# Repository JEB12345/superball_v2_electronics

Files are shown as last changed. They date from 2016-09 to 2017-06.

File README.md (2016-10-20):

# superball_v2_electronics

This repo houses all the electronic boards used in the SUPERball V2 tensegrity robot prototype.

List of PCB boards:
 - Main control board (ToDo)
 - Power control board (ToDo)
 - 10 pin Molex extension board
 - Battery connector conversion board (ToDo)

Main control board features:
 - Intel Edison Interface
 - DWM 1000 Module
 - Status LEDs (RGB and single color)
 - dsPIC33E (or lower uC?)

Power control board features:
 - Main power input of 25.2V - 22.1V
 - Regulate main power down to either 5.5 or 3.3V (do we need 5.5 regulation anymore?)
 - Backup batter support (either coincell or lipo?)
 - Power safety features all ANDed together:
   + Wireless killswitch - NRF24L01
   + manual switch
   + uC/Edison up signal
   + 24V present
 - Voltage and Current monitoring (do we need with with the Hebi motors?)
 - ??? Battery Management system per NASA requirements?

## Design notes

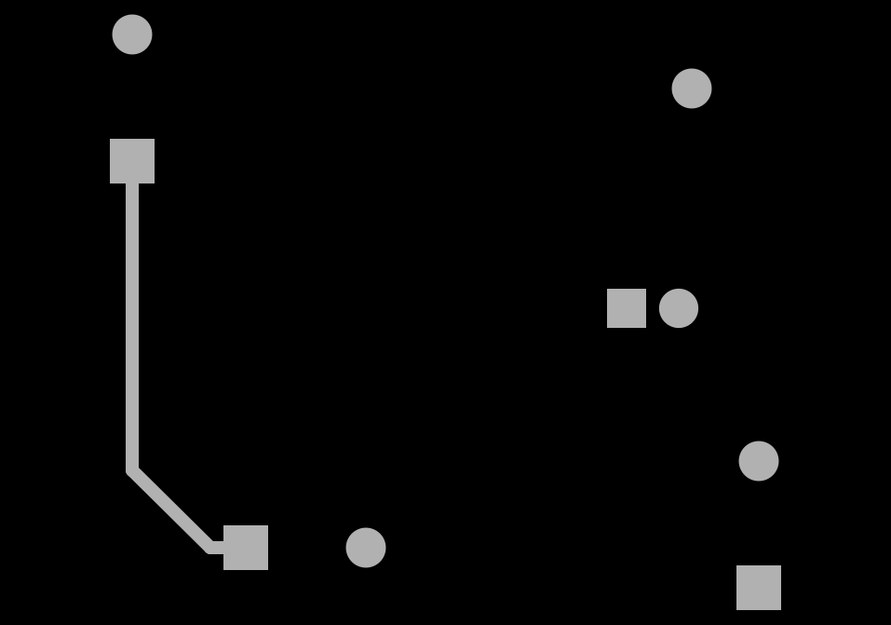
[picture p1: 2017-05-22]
main_master_dev_boards/power_systems/power_on_switch/Gerber/power_on_switch-BCu.png

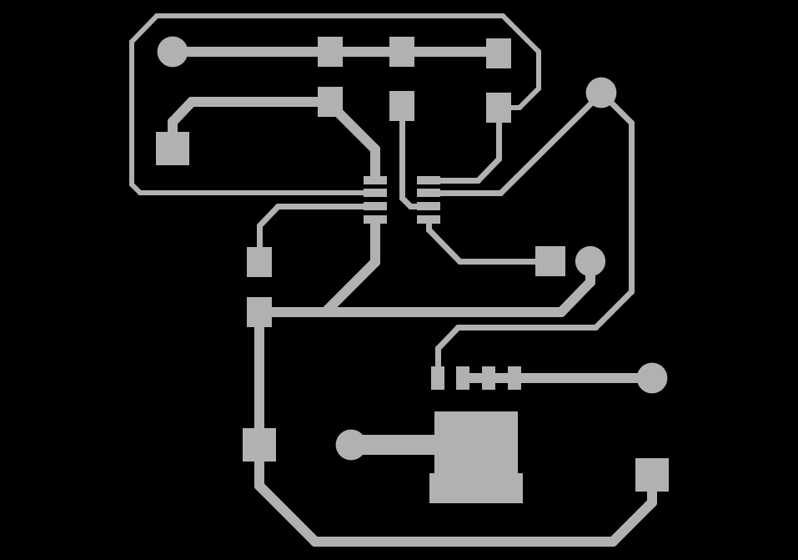
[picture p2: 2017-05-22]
main_master_dev_boards/power_systems/power_on_switch/Gerber/power_on_switch-FCu.png

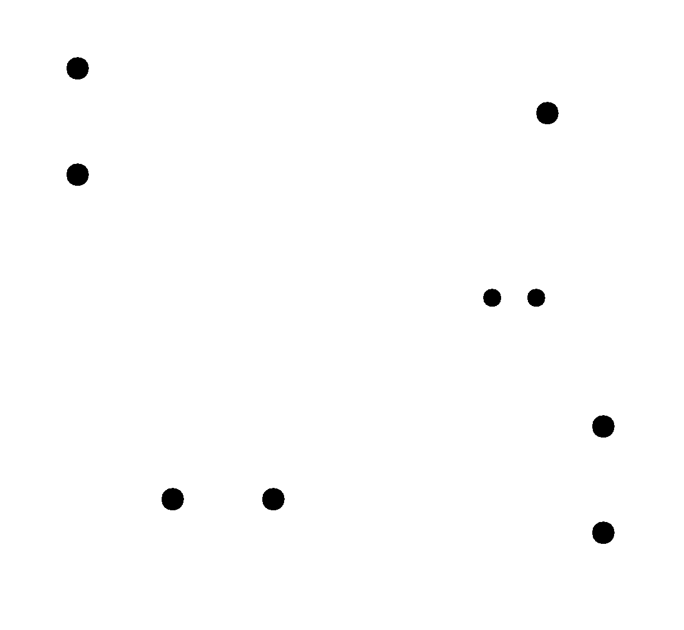
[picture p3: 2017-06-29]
main_master_dev_boards/power_systems/power_on_switch/Gerber/power_on_switch_drl_BW_edge.png

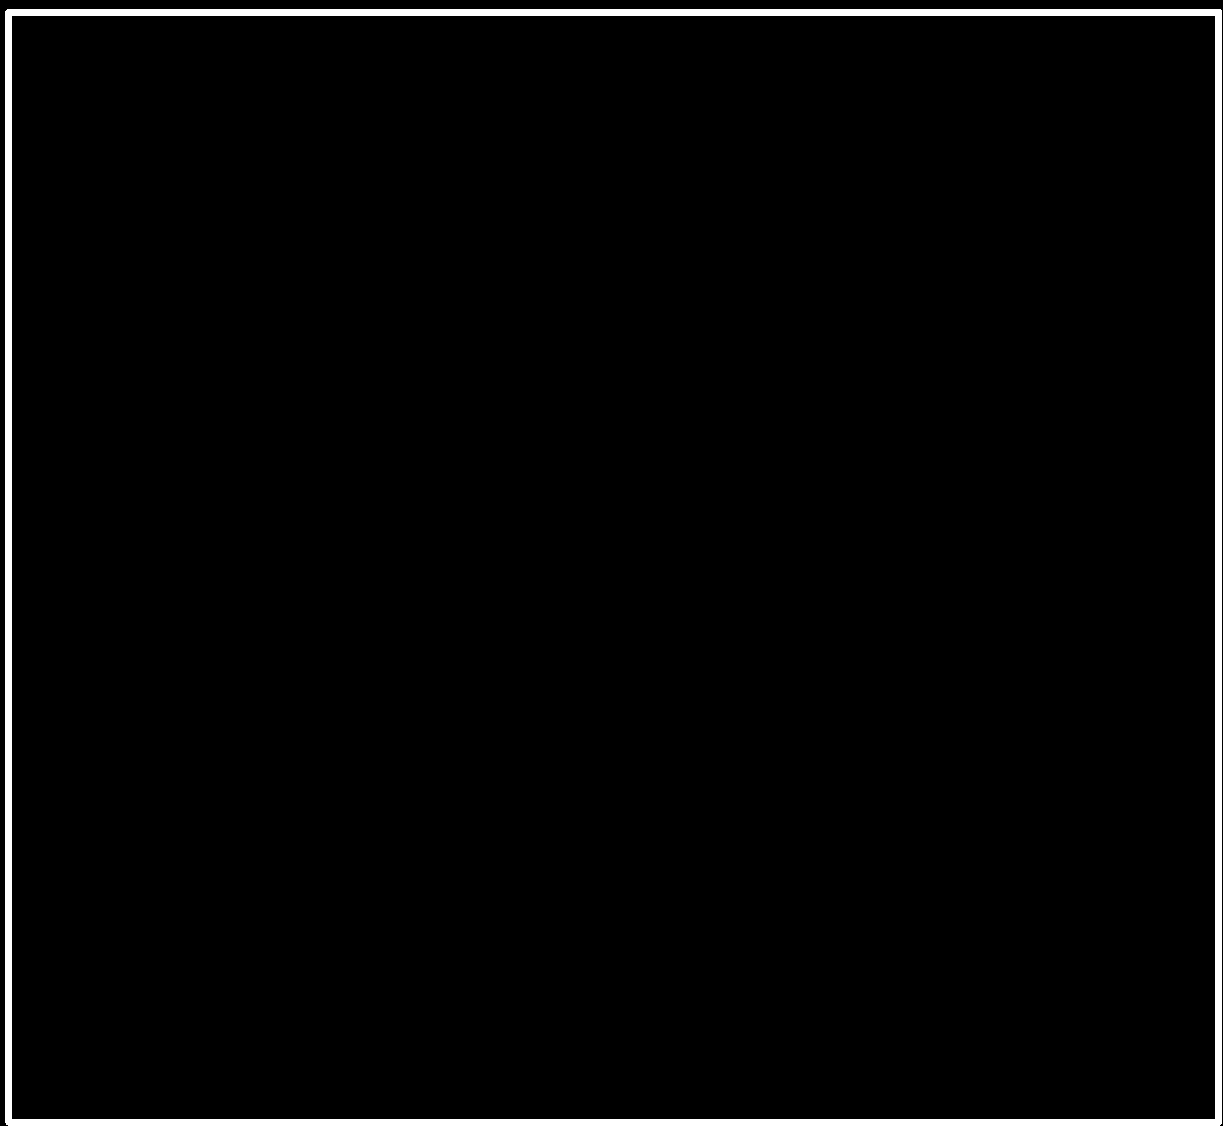
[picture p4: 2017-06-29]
main_master_dev_boards/power_systems/power_on_switch/Gerber/power_on_switch-EdgeCuts_BW.png

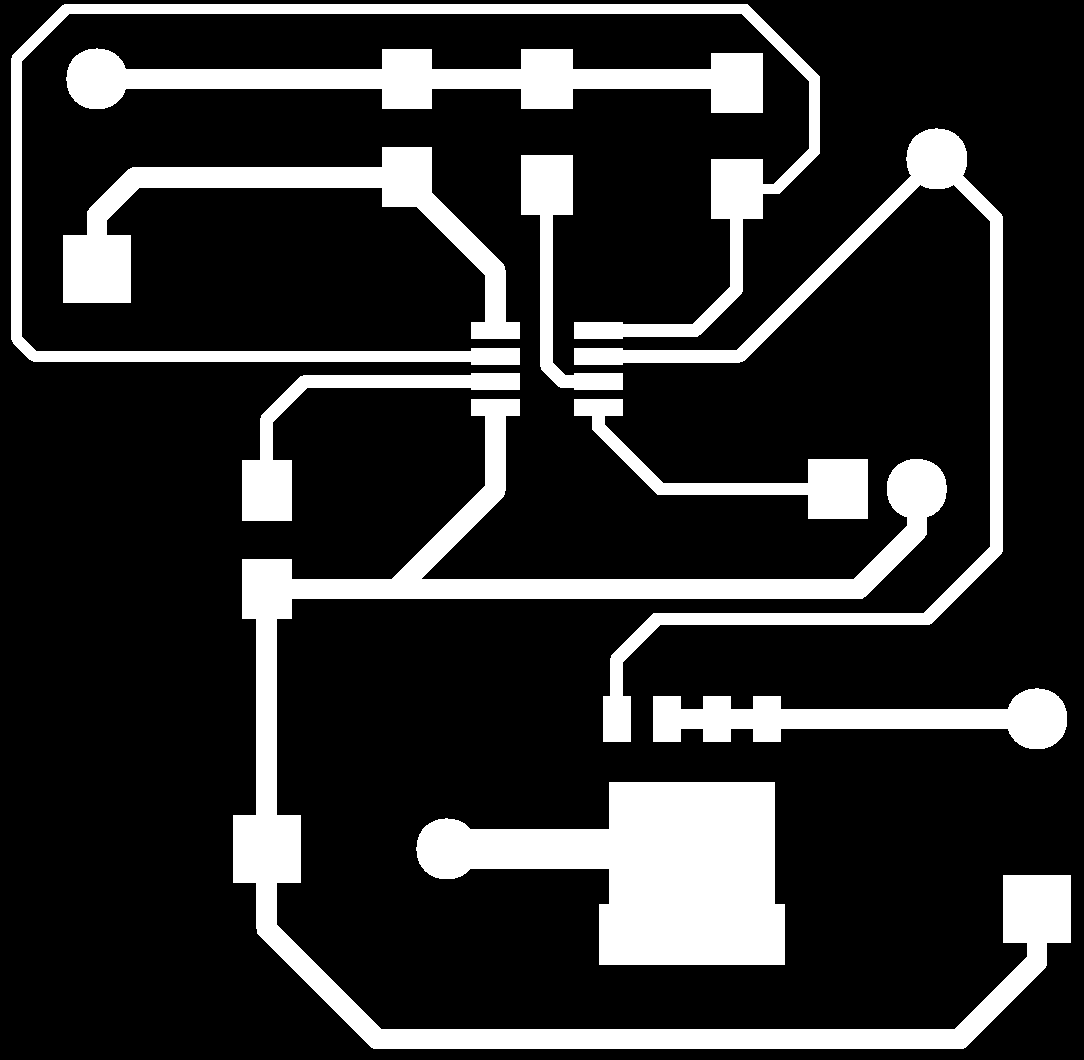
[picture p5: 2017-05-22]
main_master_dev_boards/power_systems/power_on_switch/Gerber/power_on_switch-FCu_BW.png

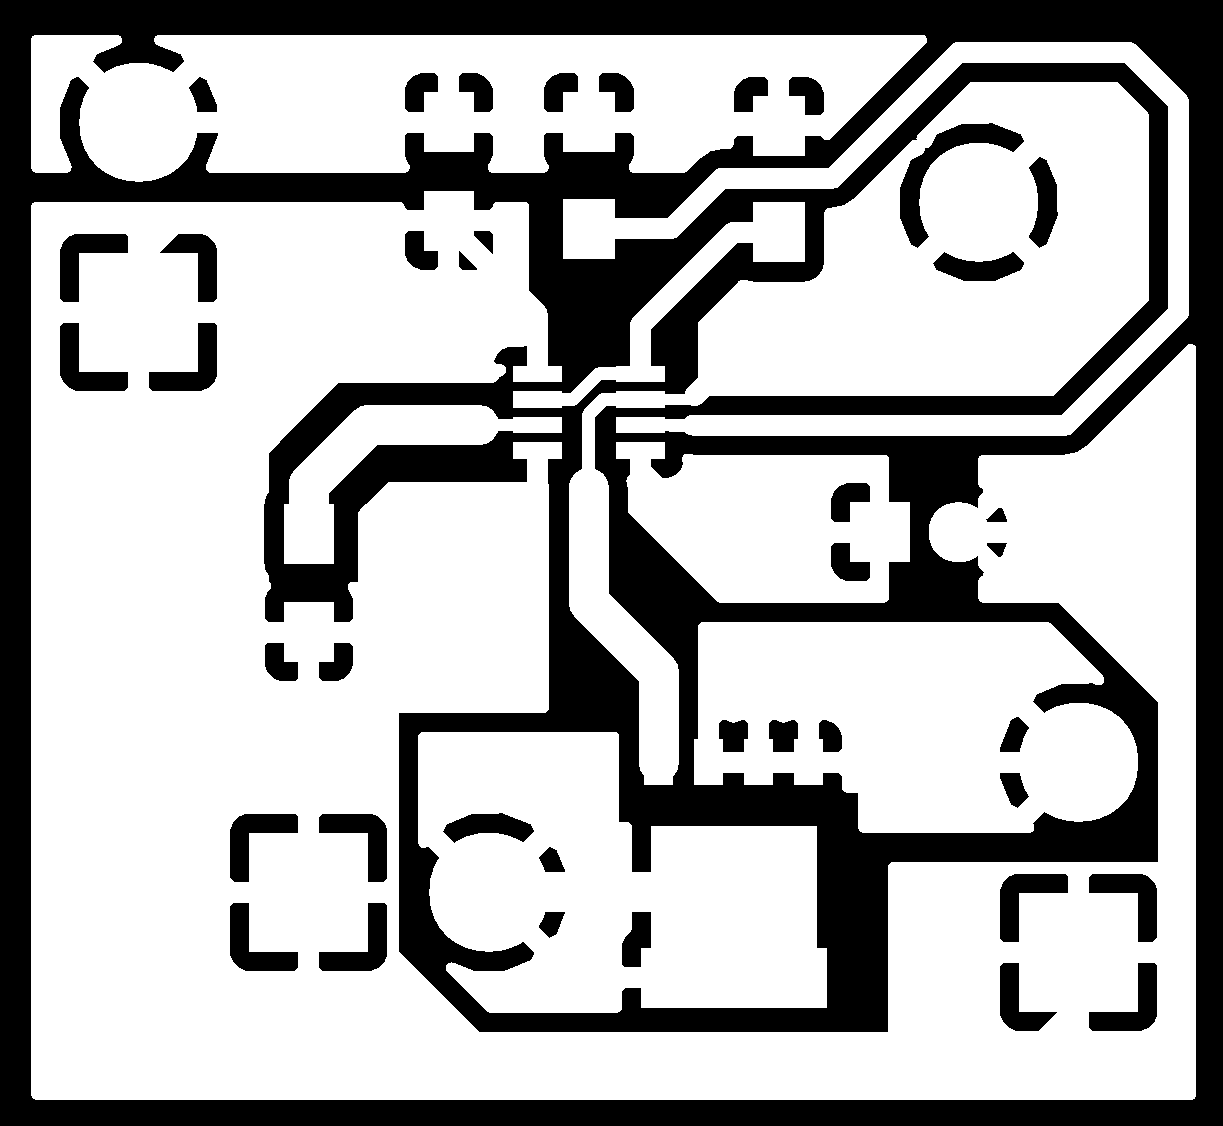
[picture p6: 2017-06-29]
main_master_dev_boards/power_systems/power_on_switch/Gerber/power_on_switch-FCu_BW_edge.png

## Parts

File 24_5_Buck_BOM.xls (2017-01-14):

Part | Manufacturer | Part Number | Quantity | Price | Attribute 1 Name | Attribute 1 Value | Attribute 2 Name | Attribute 2 Value | Attribute 3 Name | Attribute 3 Value | Footprint
Cboot | Kemet | C0805C104K5RACTU | 1 | 0.01 |  |  |  |  |  |  | 0805
Cin | TDK | C1005X5R1V225K050BC | 1 | 0.06 |  |  |  |  |  |  | 0402_065
Cout | TDK | C2012X5R1A336M125AC | 1 | 0.29 |  |  |  |  |  |  | 0805
D1 | Fairchild Semiconductor | SS24FL | 1 | 0.07 | VFatIo | 0.55V | Io | 2A | VRRM | 40V | SOD-123F
L1 | Bourns | SRN8040-150M | 1 | 0.22 | L | 15uH | DCR | 0.07Ohm | IDC | 2.4A | SRN8040
Rfbb | Yageo America | RC0603FR-0712KL | 1 | 0.01 | Resistance | 12kOhm | Tolerance | 1% | Power | 0.1W | 0603
Rfbt | Yageo America | RC0603FR-0768KL | 1 | 0.01 | Resistance | 68kOhm | Tolerance | 1% | Power | 0.1W | 0603
Rt | Vishay-Dale | CRCW040245K3FKED | 1 | 0.01 | Resistance | 45.3kOhm | Tolerance | 1% | Power | 0.063W | 0402
U1 | Texas Instruments | LMR16030PDDAR | 1 | 1.95 |  |  |  |  |  |  | DDA0008E_N
Cff | Kemet | C0805C270J5GACTU | 1 | 0.01 |  |  |  |  |  |  | 0805

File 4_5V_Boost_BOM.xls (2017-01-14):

Part | Manufacturer | Part Number | Quantity | Price | Attribute 1 Name | Attribute 1 Value | Attribute 2 Name | Attribute 2 Value | Attribute 3 Name | Attribute 3 Value | Footprint
Cin | Taiyo Yuden | JMK212BJ226MG-T | 1 | 0.05 |  |  |  |  |  |  | 0805
Cout | TDK | C3216JB1A476M | 1 | 0.3412 |  |  |  |  |  |  | 1206
Css | MuRata | GRM155R71C153KA01D | 1 | 0.01 |  |  |  |  |  |  | 0402
L1 | Vishay-Dale | IHLP2020BZER1R0M11 | 1 | 0.99 | L | 1uH | DCR | 0.018Ohm | IDC | 7A | IHLP-2020BZ
U1 | Texas Instruments | TPS61232DRCR | 1 | 0.95 |  |  |  |  |  |  | DRC0010G

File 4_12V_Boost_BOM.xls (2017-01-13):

Part | Manufacturer | Part Number | Quantity | Price | Attribute 1 Name | Attribute 1 Value | Attribute 2 Name | Attribute 2 Value | Attribute 3 Name | Attribute 3 Value | Footprint
Cbst | MuRata | GRM155R61A104KA01D | 1 | 0.01 |  |  |  |  |  |  | 402
Ccomp | MuRata | GRM033R71C181KA01D | 1 | 0.01 |  |  |  |  |  |  | 201
Ccomp2 | MuRata | GRM1555C1H9R1CA01D | 1 | 0.01 |  |  |  |  |  |  | 402
Cin | Taiyo Yuden | LMK212BJ106KG-T | 3 | 0.02 |  |  |  |  |  |  | 805
Cin2 | MuRata | GRM155R60J104KA01D | 1 | 0.01 |  |  |  |  |  |  | 402
Cout | MuRata | GRM31CR71E106KA12L | 2 | 0.05 |  |  |  |  |  |  | 1206_190
Cvcc | MuRata | GRM188R61A225KE34D | 1 | 0.02 |  |  |  |  |  |  | 603
L1 | Vishay-Dale | IHLP1616BZERR47M11 | 1 | 1.07 | L | 470nH | DCR | 0.016Ohm | IDC | 7A | IHLP-1616BZ
Rcomp | Vishay-Dale | CRCW040269K8FKED | 1 | 0.01 | Resistance | 69.8kOhm | Tolerance | 1% | Power | 0.063W | 402
Rfbb | Vishay-Dale | CRCW0402118KFKED | 1 | 0.01 | Resistance | 118kOhm | Tolerance | 1% | Power | 0.063W | 402
Rfbt | Vishay-Dale | CRCW04021M05FKED | 1 | 0.01 | Resistance | 1.05MOhm | Tolerance | 1% | Power | 0.063W | 402
Rlim | Panasonic | ERJ-8ENF1583V | 1 | 0.01 | Resistance | 158kOhm | Tolerance | 1% | Power | 0.25W | 1206
Rt | Yageo America | RC1206FR-0782KL | 1 | 0.01 | Resistance | 82kOhm | Tolerance | 1% | Power | 0.25W | 1206
U1 | Texas Instruments | TPS61089RNRR | 1 | 1.1 |  |  |  |  |  |  | RNR0011A

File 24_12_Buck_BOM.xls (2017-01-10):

Part | Manufacturer | Part Number | Quantity | Price | Footprint | Attribute 1 Name | Attribute 1 Value | Attribute 2 Name | Attribute 2 Value | Attribute 3 Name | Attribute 3 Value
Cboot | TDK | C1005X7R1H104K | 1 | 0.0172 | 402
Cff | Kemet | C0201C120K3GACTU | 1 | 0.01 | 201
Cin | MuRata | GRM31CR71H225KA88L | 1 | 0.05 | 1206_190
Cout | MuRata | GRM21BR61E475MA12L | 1 | 0.02 | 805
D1 | Fairchild Semiconductor | SS24FL | 1 | 0.07 | SOD-123F | VFatIo | 0.55V | Io | 2A | VRRM | 40V
L1 | Coilcraft | XAL4030-472MEB | 1 | 0.72 | XAL4030 | L | 4.7uH | DCR | 0.04Ohm | IDC | 4.5A
Rfbb | Vishay-Dale | CRCW040210K0FKED | 1 | 0.01 | 402 | Resistance | 10kOhm | Tolerance | 1% | Power | 0.063W
Rfbt | Vishay-Dale | CRCW0402150KFKED | 1 | 0.01 | 402 | Resistance | 150kOhm | Tolerance | 1% | Power | 0.063W
Rt | Vishay-Dale | CRCW040210K5FKED | 1 | 0.01 | 402 | Resistance | 10.5kOhm | Tolerance | 1% | Power | 0.063W
U1 | Texas Instruments | LMR16020PDDAR | 1 | 1.82 | DDA0008E_N

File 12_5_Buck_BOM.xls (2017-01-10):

Part | Manufacturer | Part Number | Quantity | Price | Attribute 1 Name | Attribute 1 Value | Attribute 2 Name | Attribute 2 Value | Attribute 3 Name | Attribute 3 Value | Footprint
Cin | Taiyo Yuden | TMK316BJ106KL-T | 1 | 0.05 |  |  |  |  |  |  | 1206
Cout | Taiyo Yuden | LMK212BJ226MG-T | 1 | 0.12 |  |  |  |  |  |  | 805
Css | MuRata | GRM1555C1E621JA01D | 1 | 0.01 |  |  |  |  |  |  | 402
Rfbb | Vishay-Dale | CRCW0402100KFKED | 1 | 0.01 | Resistance | 100kOhm | Tolerance | 1% | Power | 0.063W | 402
Rfbt | Vishay-Dale | CRCW0402523KFKED | 1 | 0.01 | Resistance | 523kOhm | Tolerance | 1% | Power | 0.063W | 402
Rpg | Vishay-Dale | CRCW0402100KFKED | 1 | 0.01 | Resistance | 100kOhm | Tolerance | 1% | Power | 0.063W | 402
U1 | Texas Instruments | TPS82130SILR | 1 | 1.9 |  |  |  |  |  |  | SIL0008D_SMD

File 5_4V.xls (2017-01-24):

Part | Manufacturer | Part Number | Quantity | Footprint | Price | Attribute 1 Name | Attribute 1 Value | Attribute 2 Name | Attribute 2 Value | Attribute 3 Name | Attribute 3 Value
Cin | Taiyo Yuden | LMK212BJ106KG-T | 1 | 805 | 0.02
Cout | MuRata | GRM32ER71C226KE18L | 1 | 1210 | 0.28
Rfbb | Vishay-Dale | CRCW0402162KFKED | 1 | 402 | 0.01 | Resistance | 162kOhm | Tolerance | 1% | Power | 0.063W
Rfbt | Vishay-Dale | CRCW0402649KFKED | 1 | 402 | 0.01 | Resistance | 649kOhm | Tolerance | 1% | Power | 0.063W
Rpg | Vishay-Dale | CRCW0402499KFKED | 1 | 402 | 0.01 | Resistance | 499kOhm | Tolerance | 1% | Power | 0.063W
U1 | Texas Instruments | TPS82084SILR | 1 | SIL0008C_SMD | 1.46

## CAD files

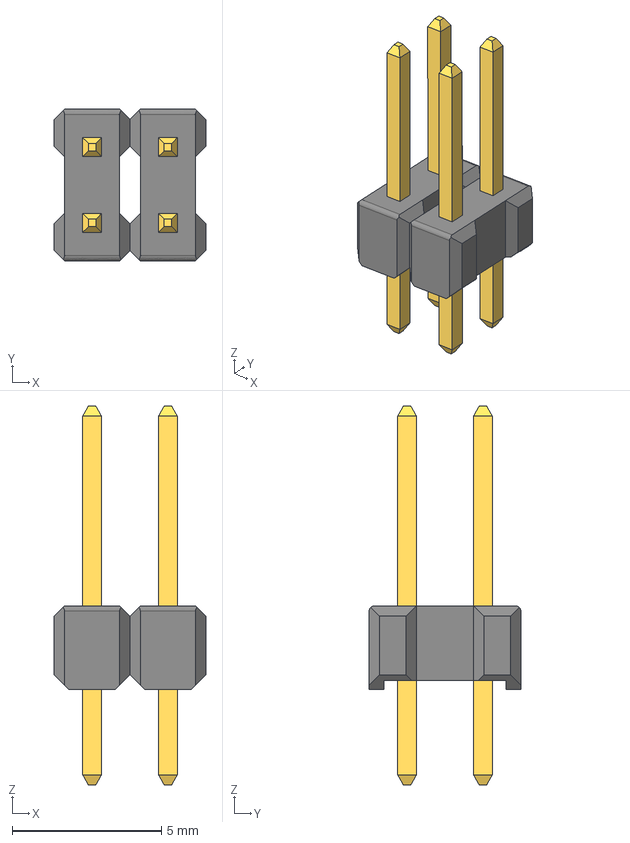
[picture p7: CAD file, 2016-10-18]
altium_converted_files/SuperBALL_Mater_Schematics/Fake-PcbDoc/Root Entry/Models/16.dat.step
5.08 x 5.08 x 12.7 mm

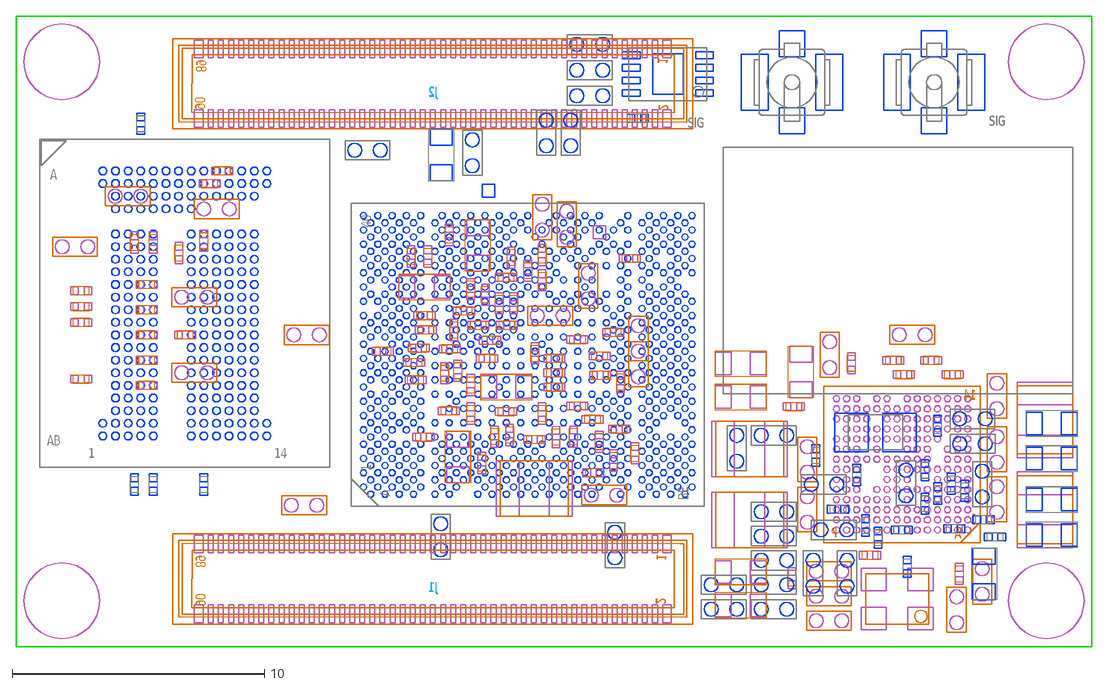
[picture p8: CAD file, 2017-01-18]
DART-SD410_REV_1-0.dxf
1
14
P
A
AB
40
BE
J2
90
89
2
J1
SIG

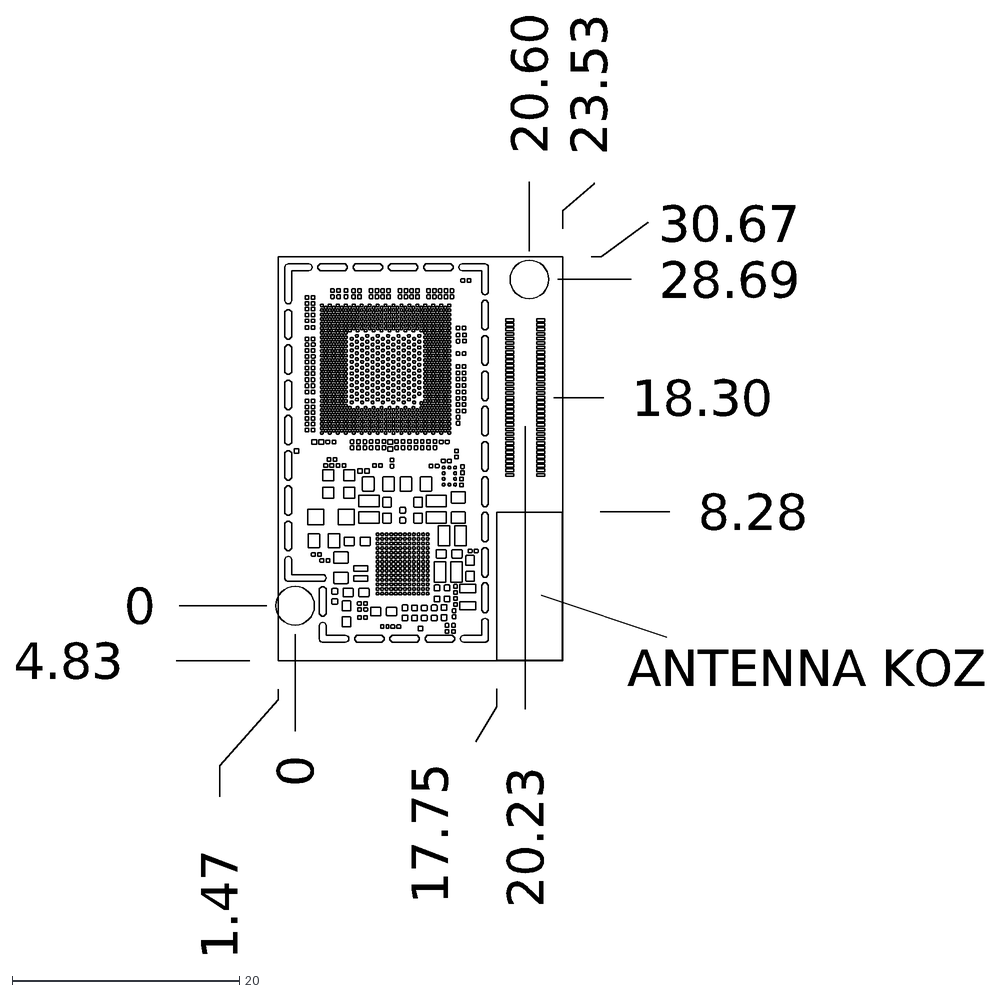
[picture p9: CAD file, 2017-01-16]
Edison/Edison_DXF.dxf
17.75
8.28
18.30
20.23
30.67
23.53
4.83
1.47
28.69
20.60
0
ANTENNA KOZ

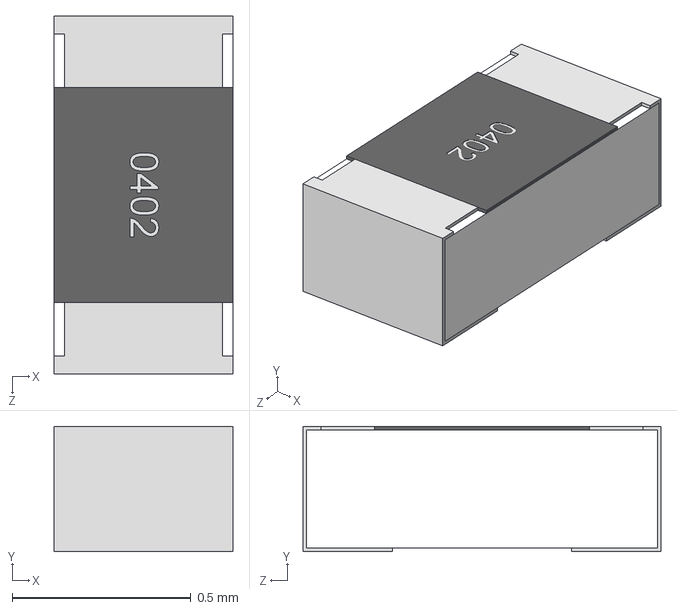
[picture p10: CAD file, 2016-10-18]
altium_converted_files/SuperBALL_Mater_Schematics/Fake-PcbDoc/Root Entry/Models/13.dat.step
0.5 x 0.35 x 1.00 mm

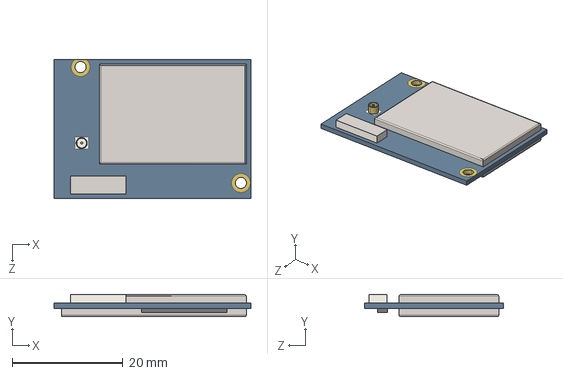
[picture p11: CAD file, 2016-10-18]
altium_converted_files/SuperBALL_Mater_Schematics/Fake-PcbDoc/Root Entry/Models/18.dat.step
35.6 x 4.01 x 25.1 mm

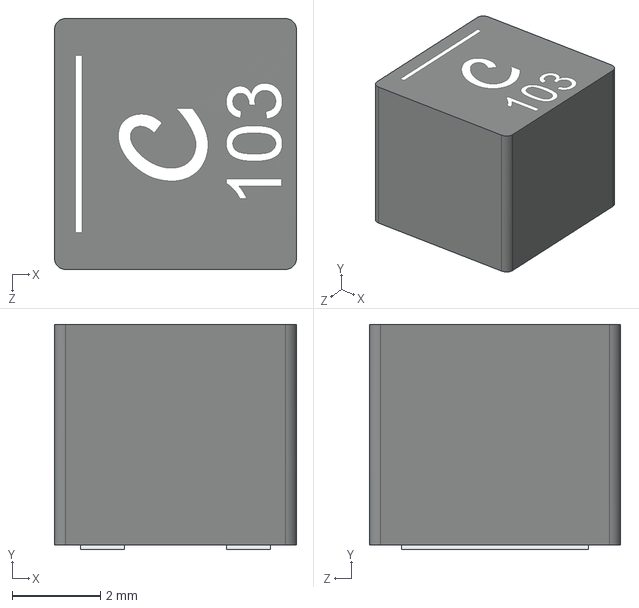
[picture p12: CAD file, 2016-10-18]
altium_converted_files/SuperBALL_Mater_Schematics/Fake-PcbDoc/Root Entry/Models/20.dat.step
5.48 x 5.10 x 5.68 mm

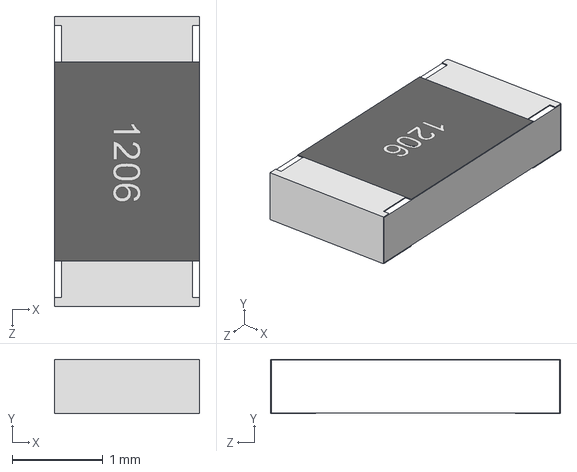
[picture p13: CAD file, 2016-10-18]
altium_converted_files/SuperBALL_Mater_Schematics/Fake-PcbDoc/Root Entry/Models/4.dat.step
1.60 x 0.6 x 3.20 mm

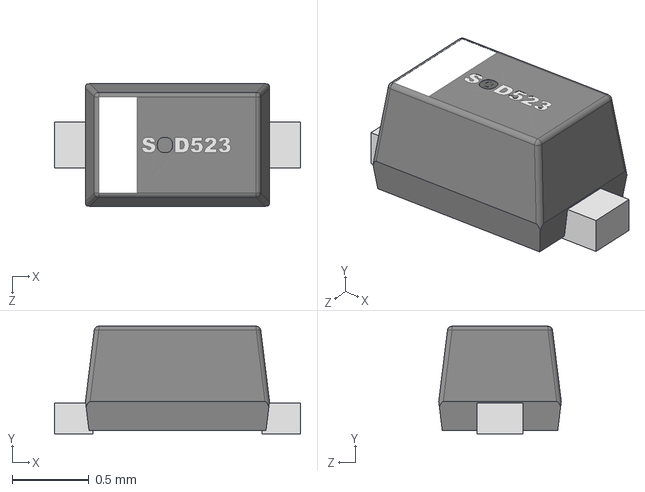
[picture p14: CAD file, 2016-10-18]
altium_converted_files/SuperBALL_Mater_Schematics/Fake-PcbDoc/Root Entry/Models/11.dat.step
1.60 x 0.7 x 0.798 mm

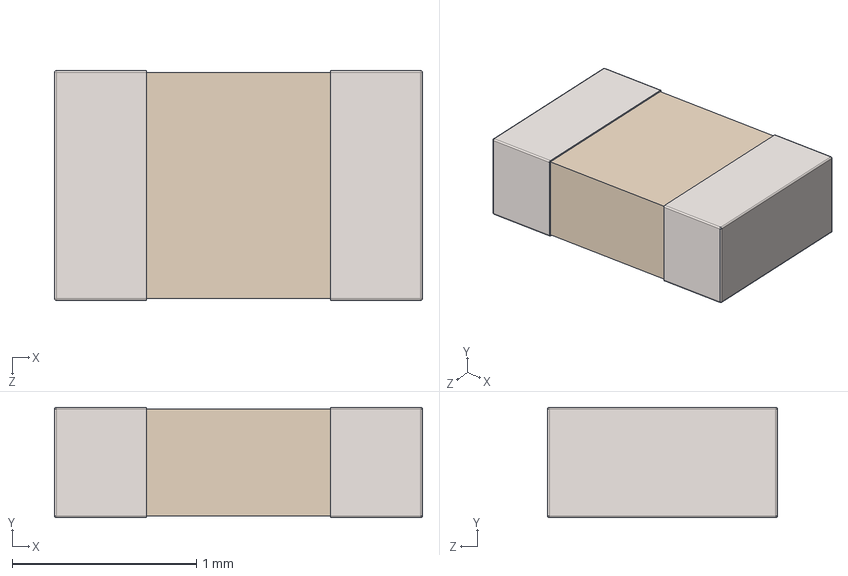
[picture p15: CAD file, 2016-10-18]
altium_converted_files/SuperBALL_Mater_Schematics/Fake-PcbDoc/Root Entry/Models/2.dat.step
2.00 x 0.6 x 1.25 mm

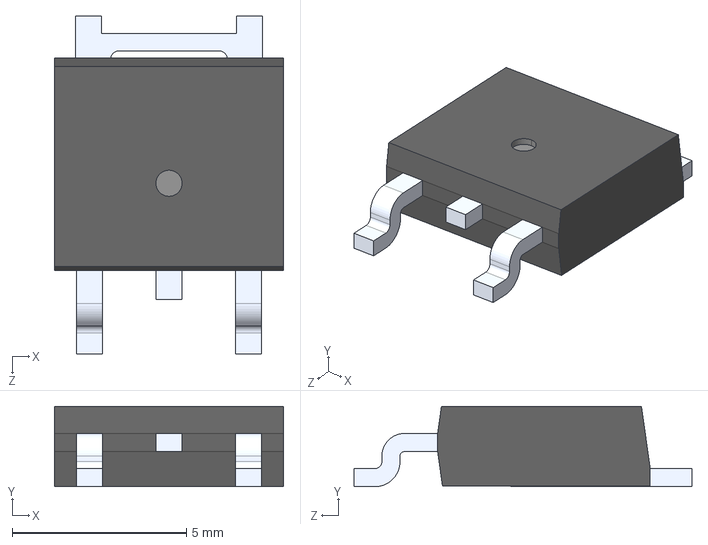
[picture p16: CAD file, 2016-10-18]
altium_converted_files/SuperBALL_Mater_Schematics/Fake-PcbDoc/Root Entry/Models/12.dat.step
6.58 x 2.31 x 9.70 mm

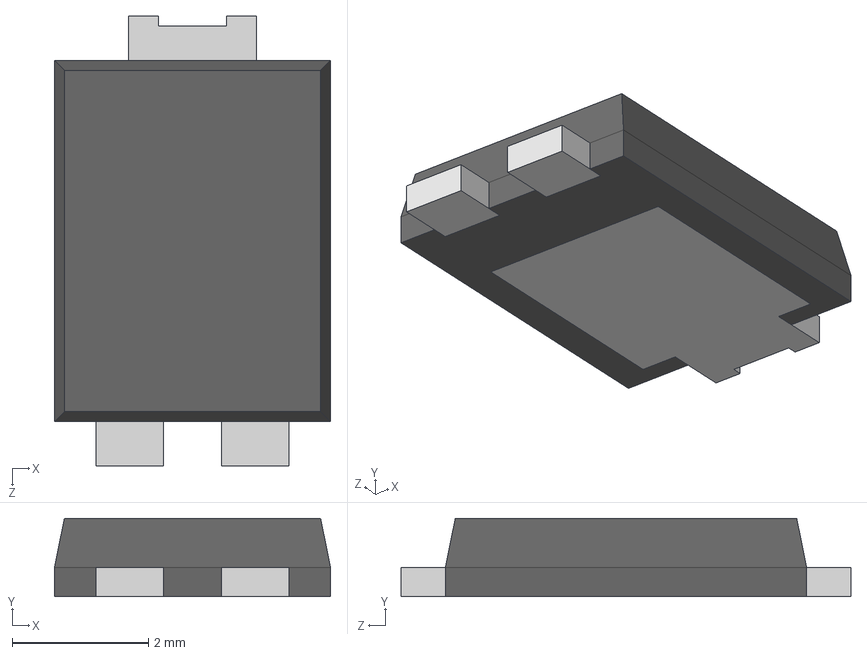
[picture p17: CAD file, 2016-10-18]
altium_converted_files/SuperBALL_Mater_Schematics/Fake-PcbDoc/Root Entry/Models/8.dat.step
4.05 x 1.15 x 6.60 mm
User Library-PowerDI-5_1_1
User Library-PowerDI-5_2_1
User Library-PowerDI-5_3_1
User Library-PowerDI-5_4_1

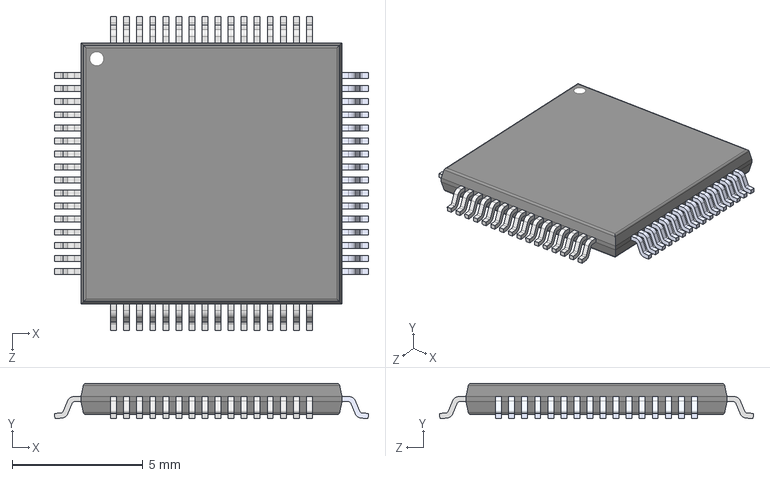
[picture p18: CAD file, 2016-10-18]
altium_converted_files/SuperBALL_Mater_Schematics/Fake-PcbDoc/Root Entry/Models/14.dat.step
12.0 x 1.35 x 12.0 mm

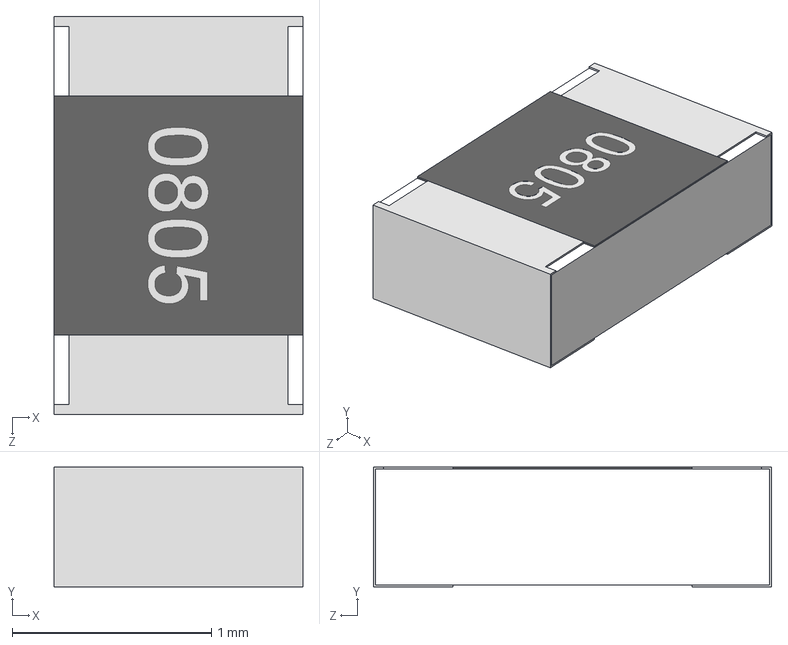
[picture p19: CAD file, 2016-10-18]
altium_converted_files/SuperBALL_Mater_Schematics/Fake-PcbDoc/Root Entry/Models/5.dat.step
1.25 x 0.6 x 2.00 mm

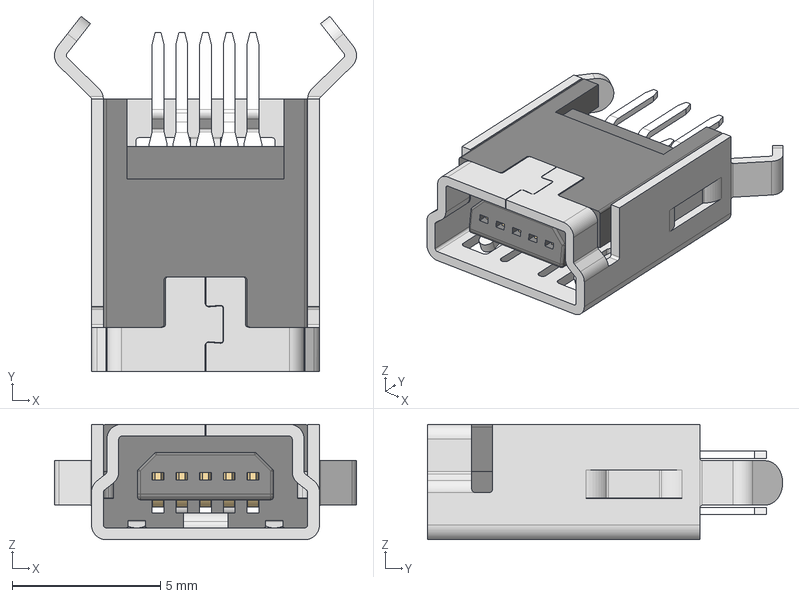
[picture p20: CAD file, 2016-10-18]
altium_converted_files/SuperBALL_Mater_Schematics/Fake-PcbDoc/Root Entry/Models/17.dat.step
10.2 x 12.0 x 3.90 mm
Shielding
Insulator
Pin_1 x 3
Pin_2 x 2

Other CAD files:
main_master_board/main_master_board1.SLDPRT
altium_converted_files/SuperBALL_Mater_Schematics/Fake-PcbDoc/Root Entry/Models/9.dat.step
altium_converted_files/SuperBALL_Mater_Schematics/Fake-PcbDoc/Root Entry/Models/19.dat.step
altium_converted_files/SuperBALL_Mater_Schematics/Fake-PcbDoc/Root Entry/Models/0.dat.step
Edison/H38489-005_R02 _emn.stp
altium_converted_files/SuperBALL_Mater_Schematics/Fake-PcbDoc/Root Entry/Models/1.dat.step
altium_converted_files/SuperBALL_Mater_Schematics/Fake-PcbDoc/Root Entry/Models/10.dat.step
altium_converted_files/SuperBALL_Mater_Schematics/Fake-PcbDoc/Root Entry/Models/15.dat.step
altium_converted_files/SuperBALL_Mater_Schematics/Fake-PcbDoc/Root Entry/Models/3.dat.step
altium_converted_files/SuperBALL_Mater_Schematics/Fake-PcbDoc/Root Entry/Models/6.dat.step
altium_converted_files/SuperBALL_Mater_Schematics/Fake-PcbDoc/Root Entry/Models/7.dat.step

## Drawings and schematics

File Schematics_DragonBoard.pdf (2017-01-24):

Size D | Document Number <Doc> | Rev A

Date: Monday, August 31, 2015 Monday, August 31, 2015 Monday, August 31, 2015 | Sheet 1 1 1 of 33 33 33

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
A | A
B | B
C | C
D | D
33 | \ | WGR7640 - GPS
32 | \ | WCN3620 - PWR / GND
31 | \ | WCN3620 - RF / CONTROL
30 | \ | JTAG / UART / ANALOG EXPANSION
29 | \ | HS / LS EXPANSION CONNECTORS
28 | \ | SWITCHES/LEDS
27 | \ | DISPLAY - DSI TO HDMI BRIDGE
26 | \ | DISPLAY - DSI SWITCH
25 | \ | USB - CONNECTORS
24 | \ | USB - SWITCH / HUB
23 | \ | MEMORY - USD CONNECTOR
22 | \ | MEMORY - LPDDR3 + EMMC - POWER
21 | \ | MEMORY - LPDDR3 + EMMC - CONTR
20 | \ | PM8916 - AUDIO
19 | \ | PM8916 - LDOS
18 | \ | PM8916 - SMPS
17 | \ | PM8916 - CHARGER/GPIOS/MPPS
16 | \ | PM8916 - CONTROL/CLOCKS
15 | \ | EXTERNAL BUCK REGULATORS
14 | \ | APQ8016 - DECOUPLING
13 | \ | APQ8016 - GND
12 | \ | APQ8016 - PWR3
11 | \ | APQ8016 - PWR2
10 | \ | APQ8016 - PWR1
9 | \ | APQ8016 - RF INTERFACE
8 | \ | APQ8016 - MIPI CSI/DSI
7 | \ | APQ8016 - BOOT CONFIG SW
6 | \ | APQ8016 - GPIO 74-121 / DNC
5 | \ | APQ8016 - GPIO 0-73
4 | \ | APQ8016 - EBI0-LPDDR3
3 | \ | APQ8016 - CONTROL
2 | \ | TABLE_OF_CONTENTS
1 | \ | TITLE
SHEET BLOCK | SCHEMATIC | SHEET BLOCK | SCHEMATIC | SHEET BLOCK | SCHEMATIC | SHEET BLOCK | SCHEMATIC
Monday, August 31, 2015 | 2 | 33
Monday, August 31, 2015 | 2 | 33
Monday, August 31, 2015 | 2 | 33

# APQ8016 - CONTROL

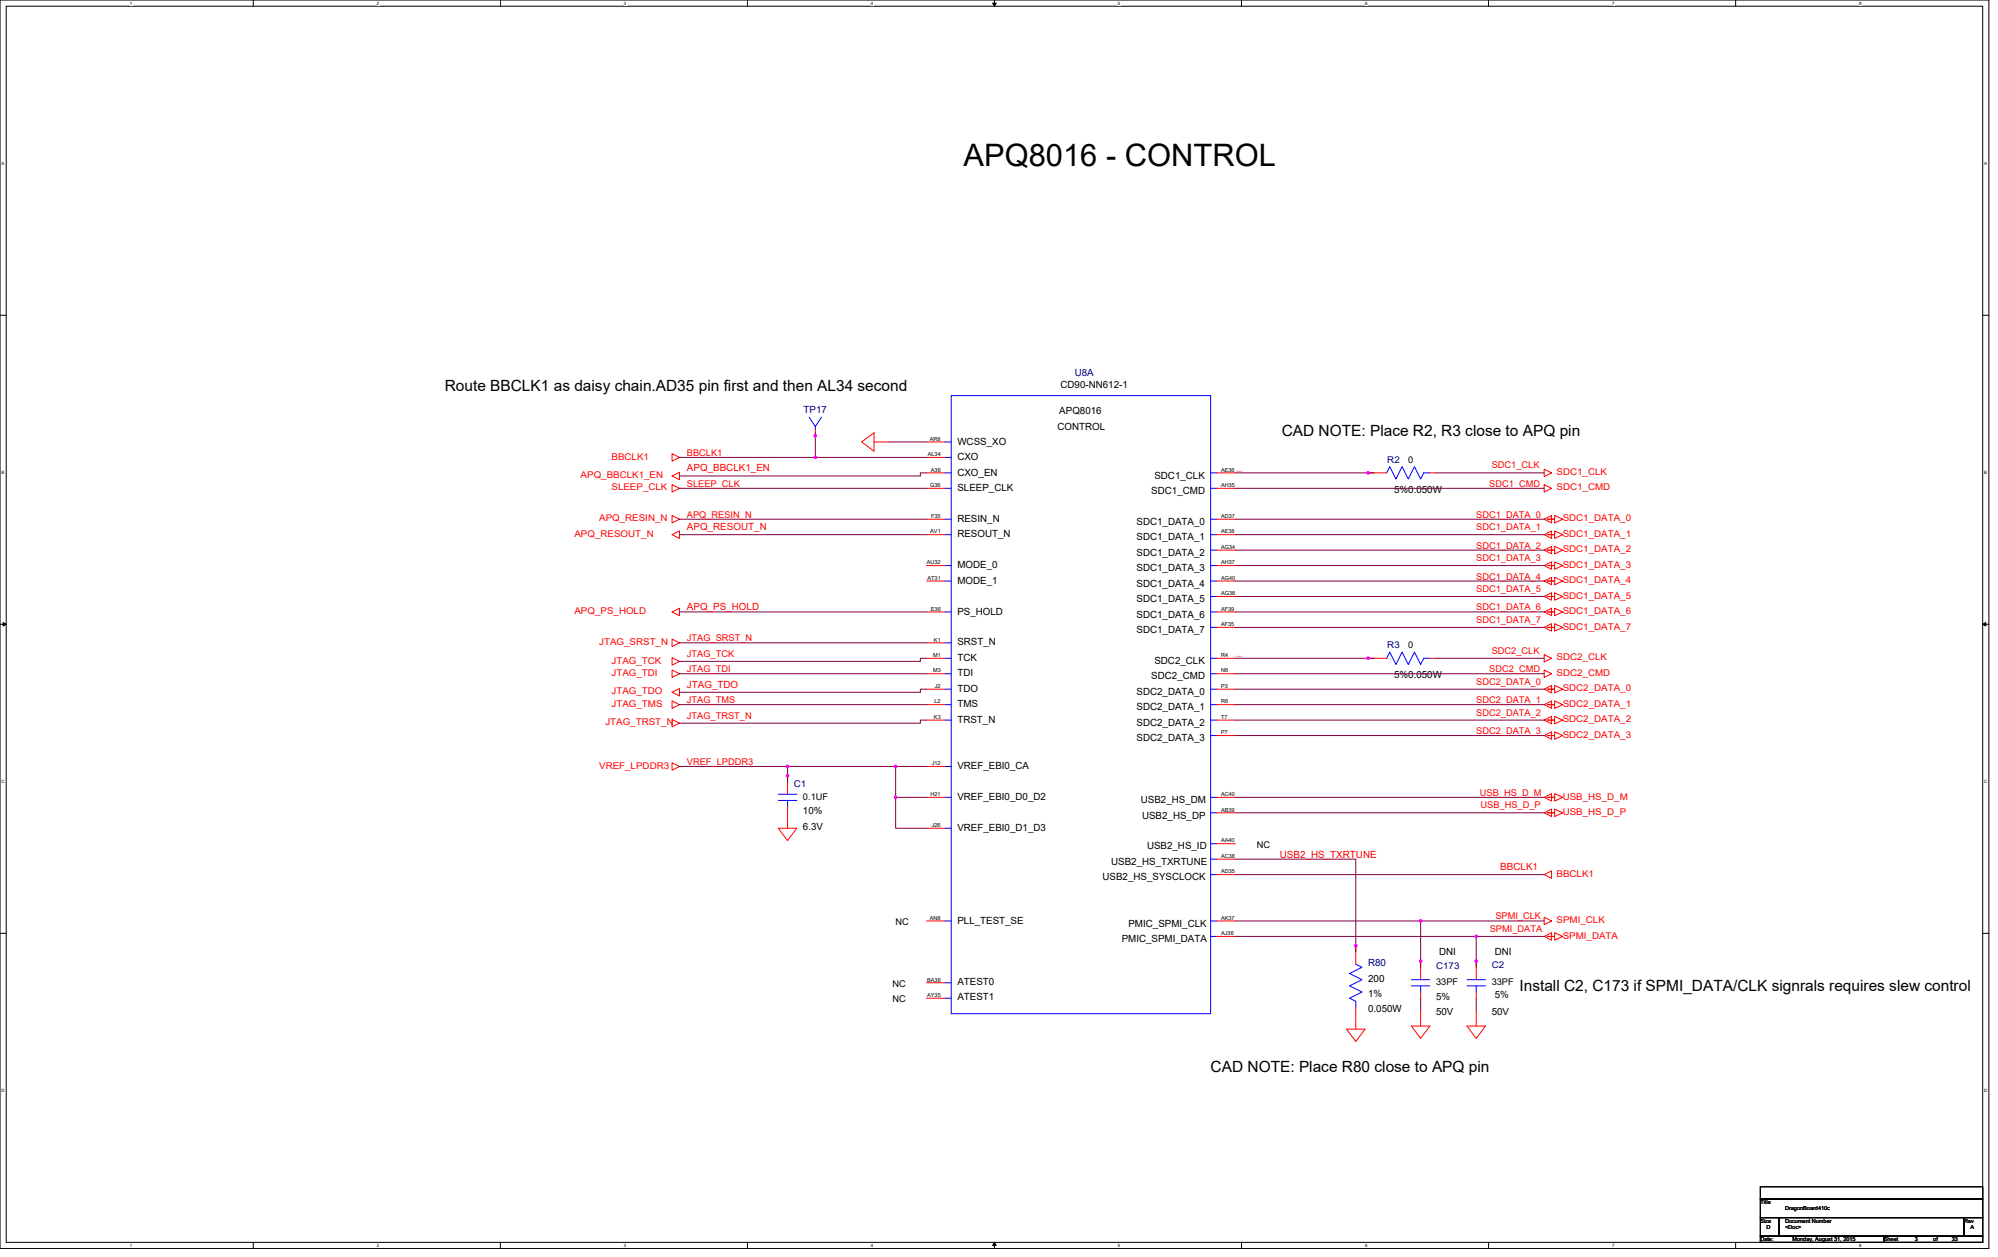
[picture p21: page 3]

Route BBCLK1 as daisy chain.AD35 pin first and then AL34 second

CAD NOTE: Place R2, R3 close to APQ pin

CAD NOTE: Place R80 close to APQ pin

# APQ8016 - EBI0-LPDDR3

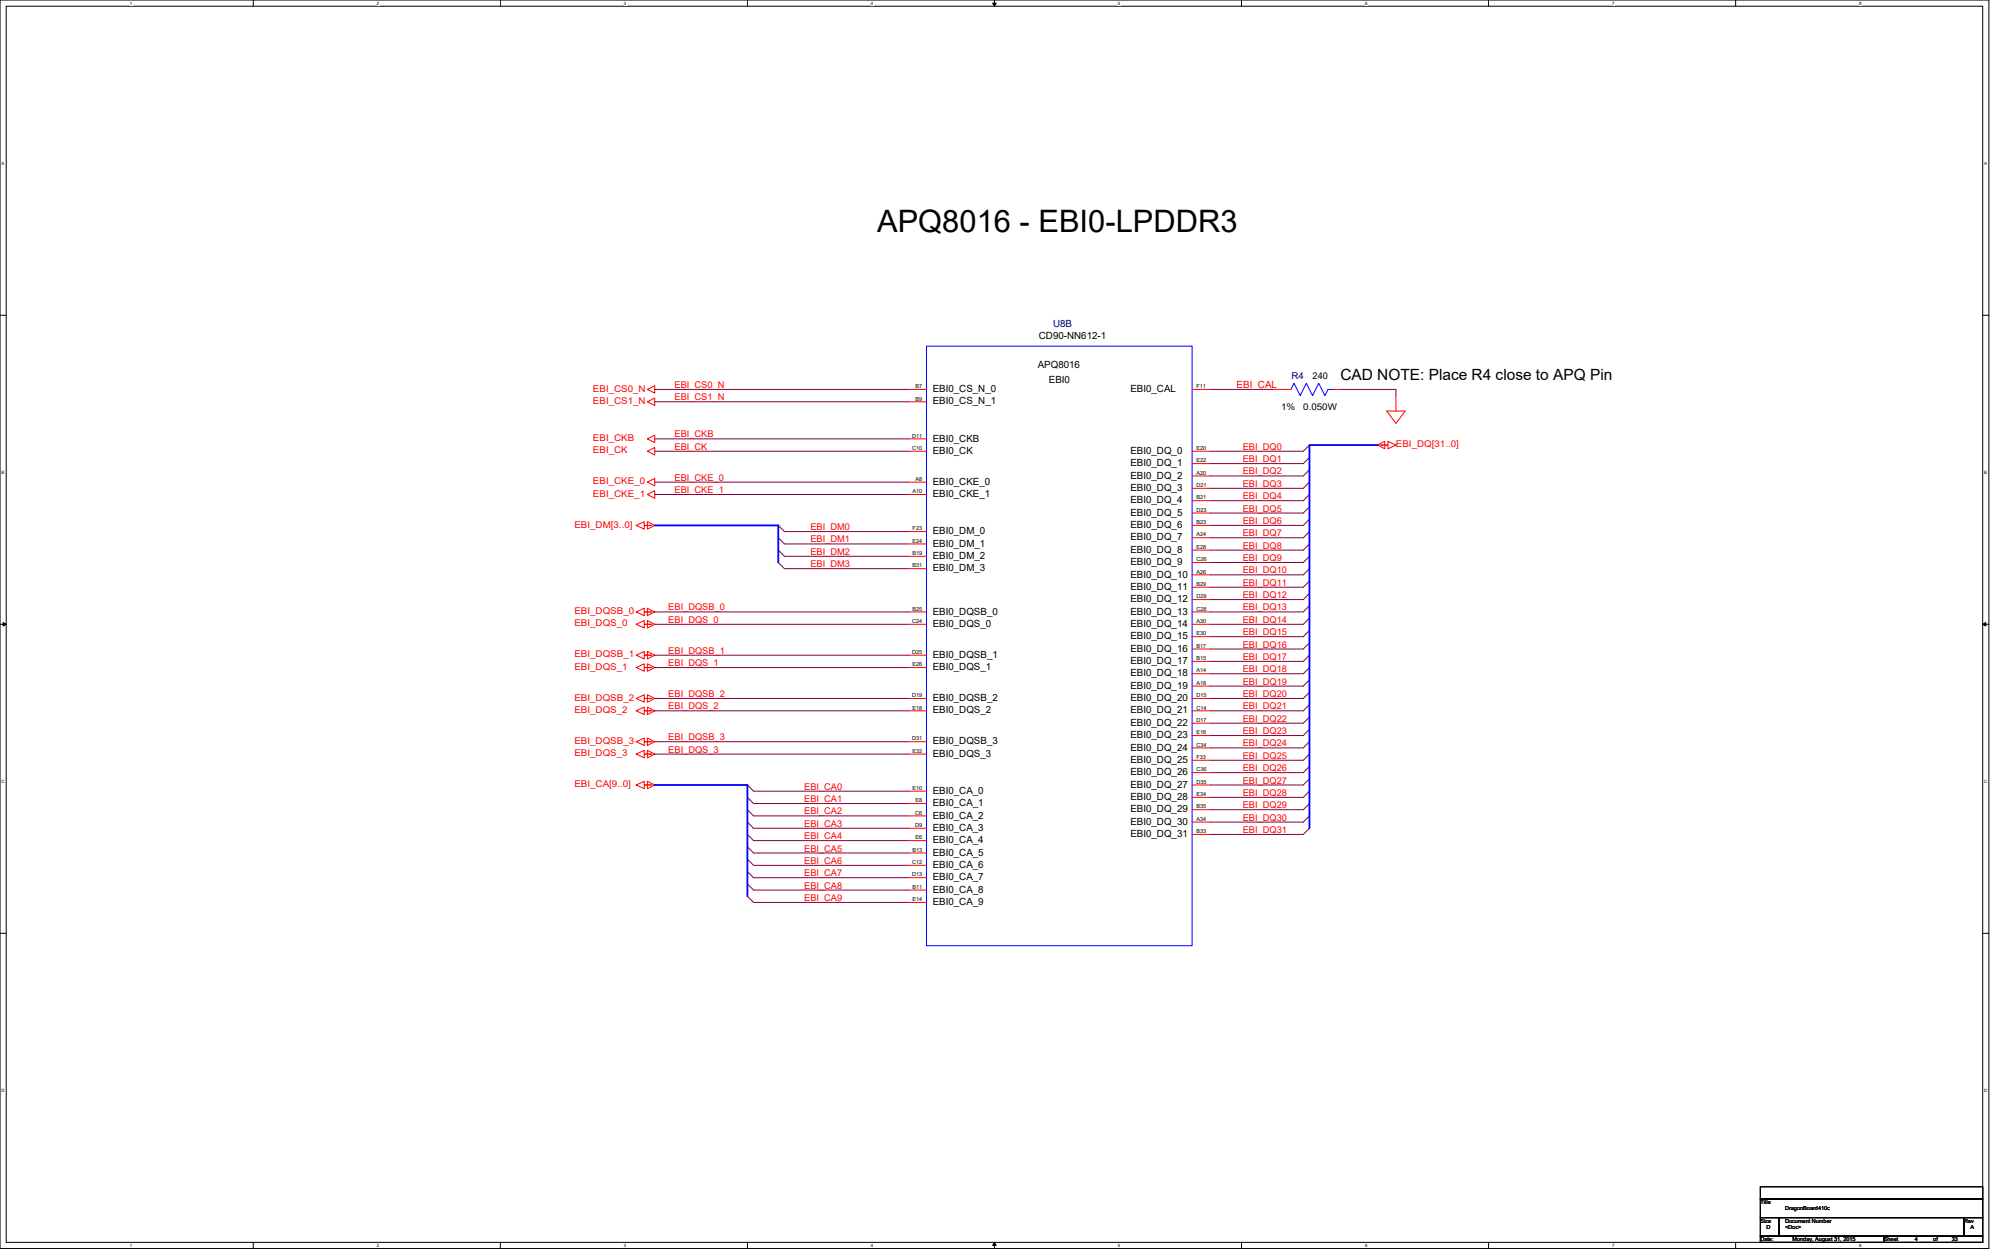
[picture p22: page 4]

CAD NOTE: Place R4 close to APQ Pin

# APQ8016 - GPIO 0-73

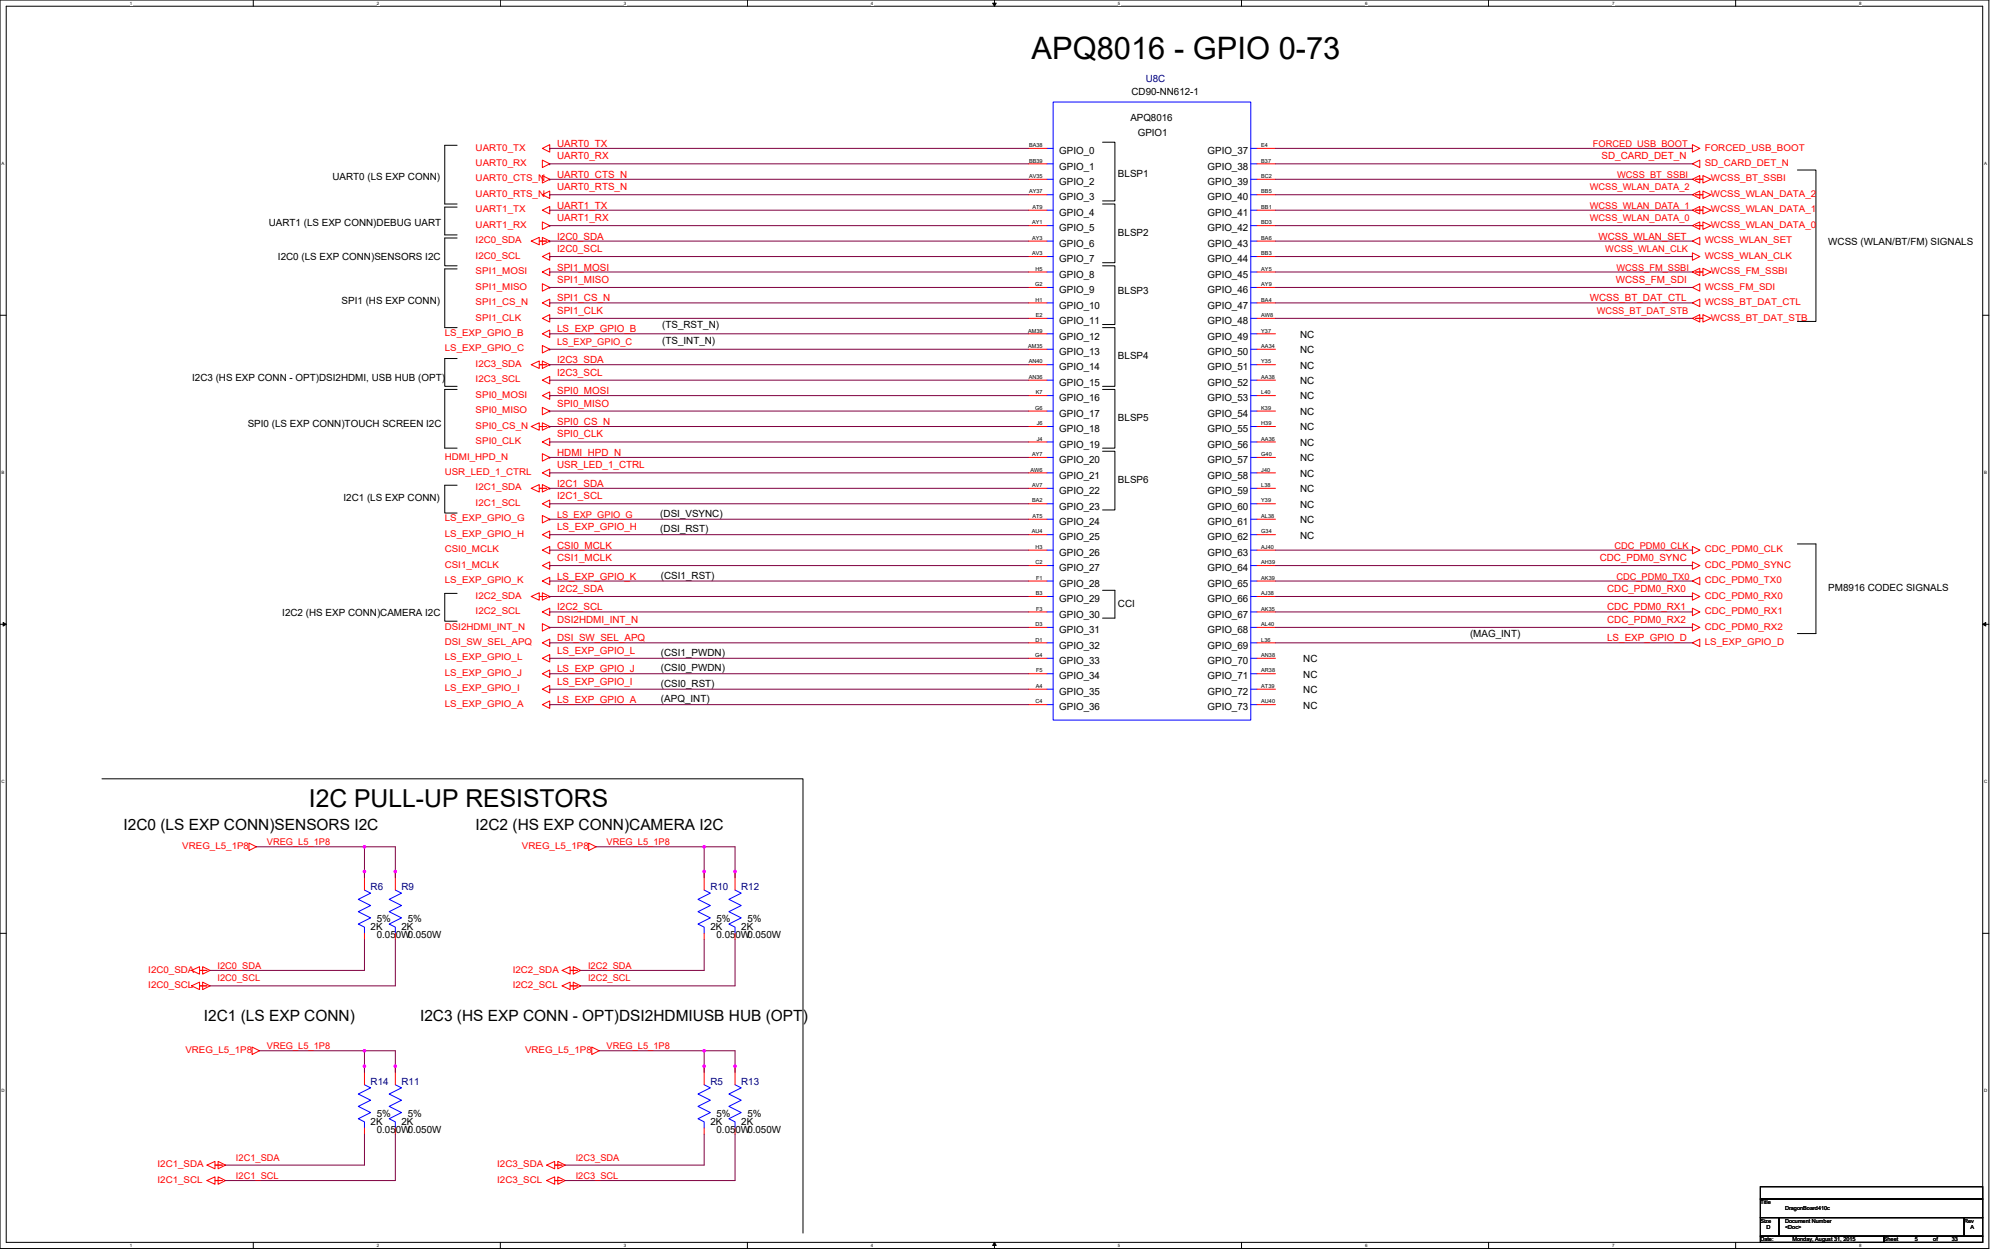
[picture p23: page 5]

UART1 (LS EXP CONN)DEBUG UART

WCSS (WLAN/BT/FM) SIGNALS

I2C0 (LS EXP CONN)SENSORS I2C

I2C3 (HS EXP CONN - OPT)DSI2HDMI, USB HUB (OPT)

SPI0 (LS EXP CONN)TOUCH SCREEN I2C

I2C2 (HS EXP CONN)CAMERA I2C

I2C3 (HS EXP CONN - OPT)DSI2HDMIUSB HUB (OPT)

# APQ8016 - GPIO 74-121 / DNC

# APQ8016 - BOOT CONFIG SW

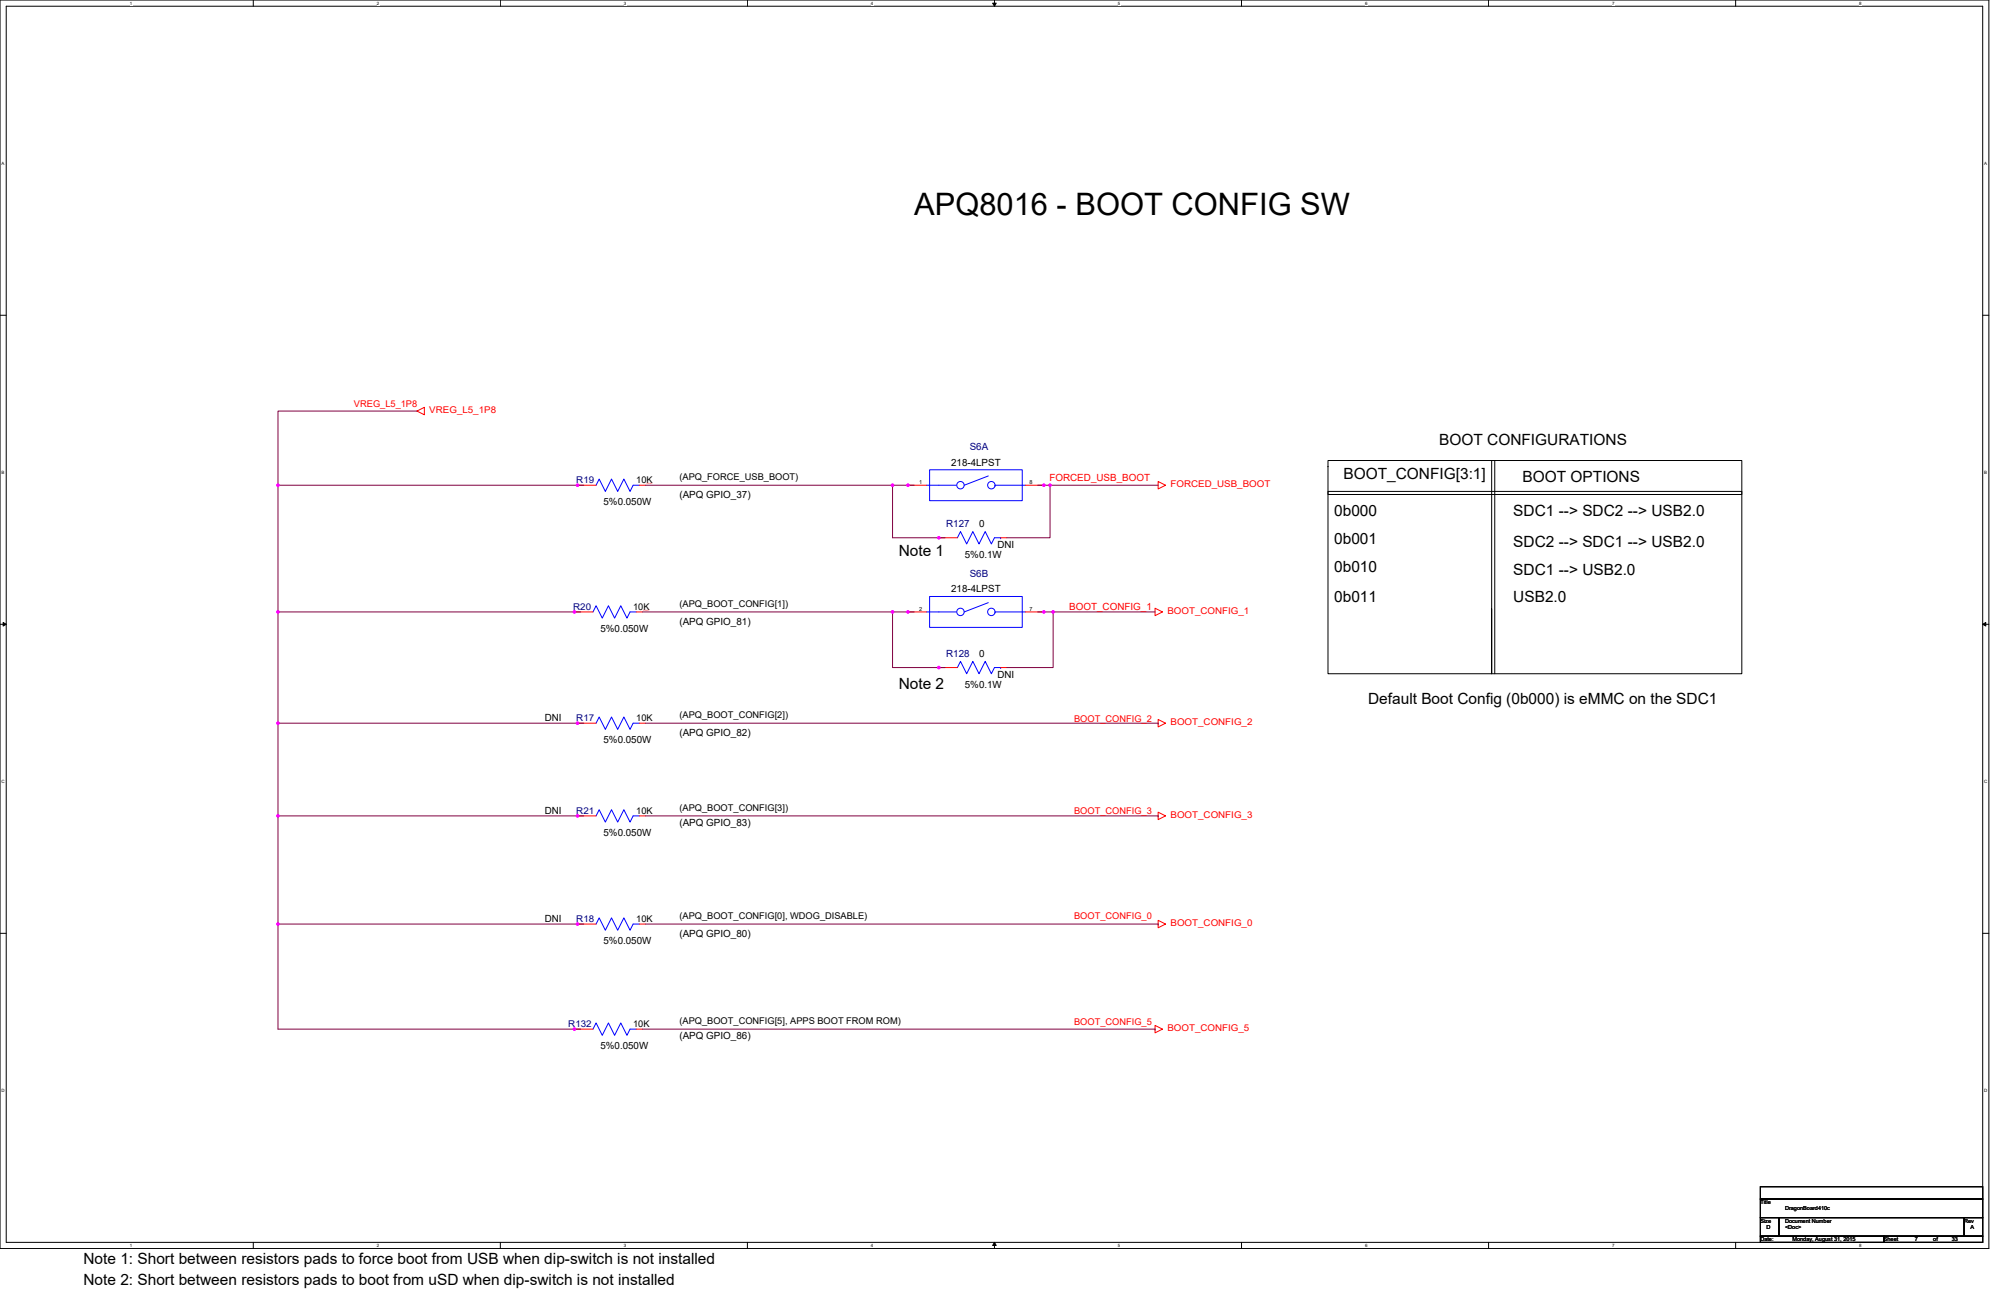
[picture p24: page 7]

Default Boot Config (0b000) is eMMC on the SDC1

(APQ_BOOT_CONFIG[5], APPS BOOT FROM ROM)
(APQ GPIO_86)

Note 1: Short between resistors pads to force boot from USB when dip-switch is not installed
Note 2: Short between resistors pads to boot from uSD when dip-switch is not installed

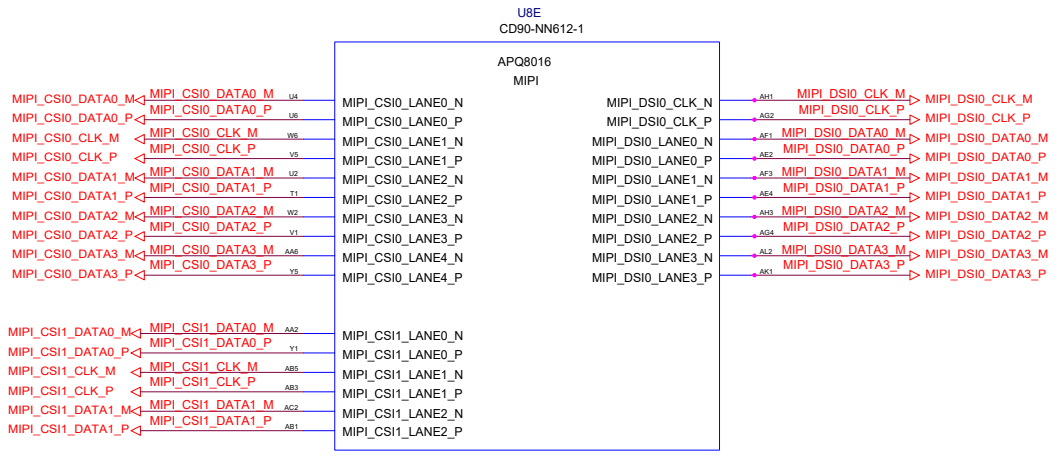
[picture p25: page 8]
MIPI_CSI1_DATA1_P; MIPI_CSI1_DATA1_M; MIPI_CSI1_CLK_P; MIPI_CSI1_CLK_M; MIPI_CSI1_DATA0_P; MIPI_CSI1_DATA0_M; MIPI_CSI0_DATA3_P; MIPI_CSI0_DATA3_M; MIPI_CSI0_DATA2_P; MIPI_CSI0_DATA2_M; MIPI_CSI0_DATA1_P; MIPI_CSI0_DATA1_M; MIPI_CSI0_CLK_P; MIPI_CSI0_CLK_M; MIPI_CSI0_DATA0_P; MIPI_CSI0_DATA0_M; MIPI_DSI0_DATA3_P; MIPI_DSI0_DATA3_M; MIPI_DSI0_DATA2_P; MIPI_DSI0_DATA2_M; MIPI_DSI0_DATA1_P; MIPI_DSI0_DATA1_M; MIPI_DSI0_DATA0_P; MIPI_DSI0_DATA0_M; MIPI_DSI0_CLK_P; MIPI_DSI0_CLK_M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

# APQ8016 - RF INTERFACE

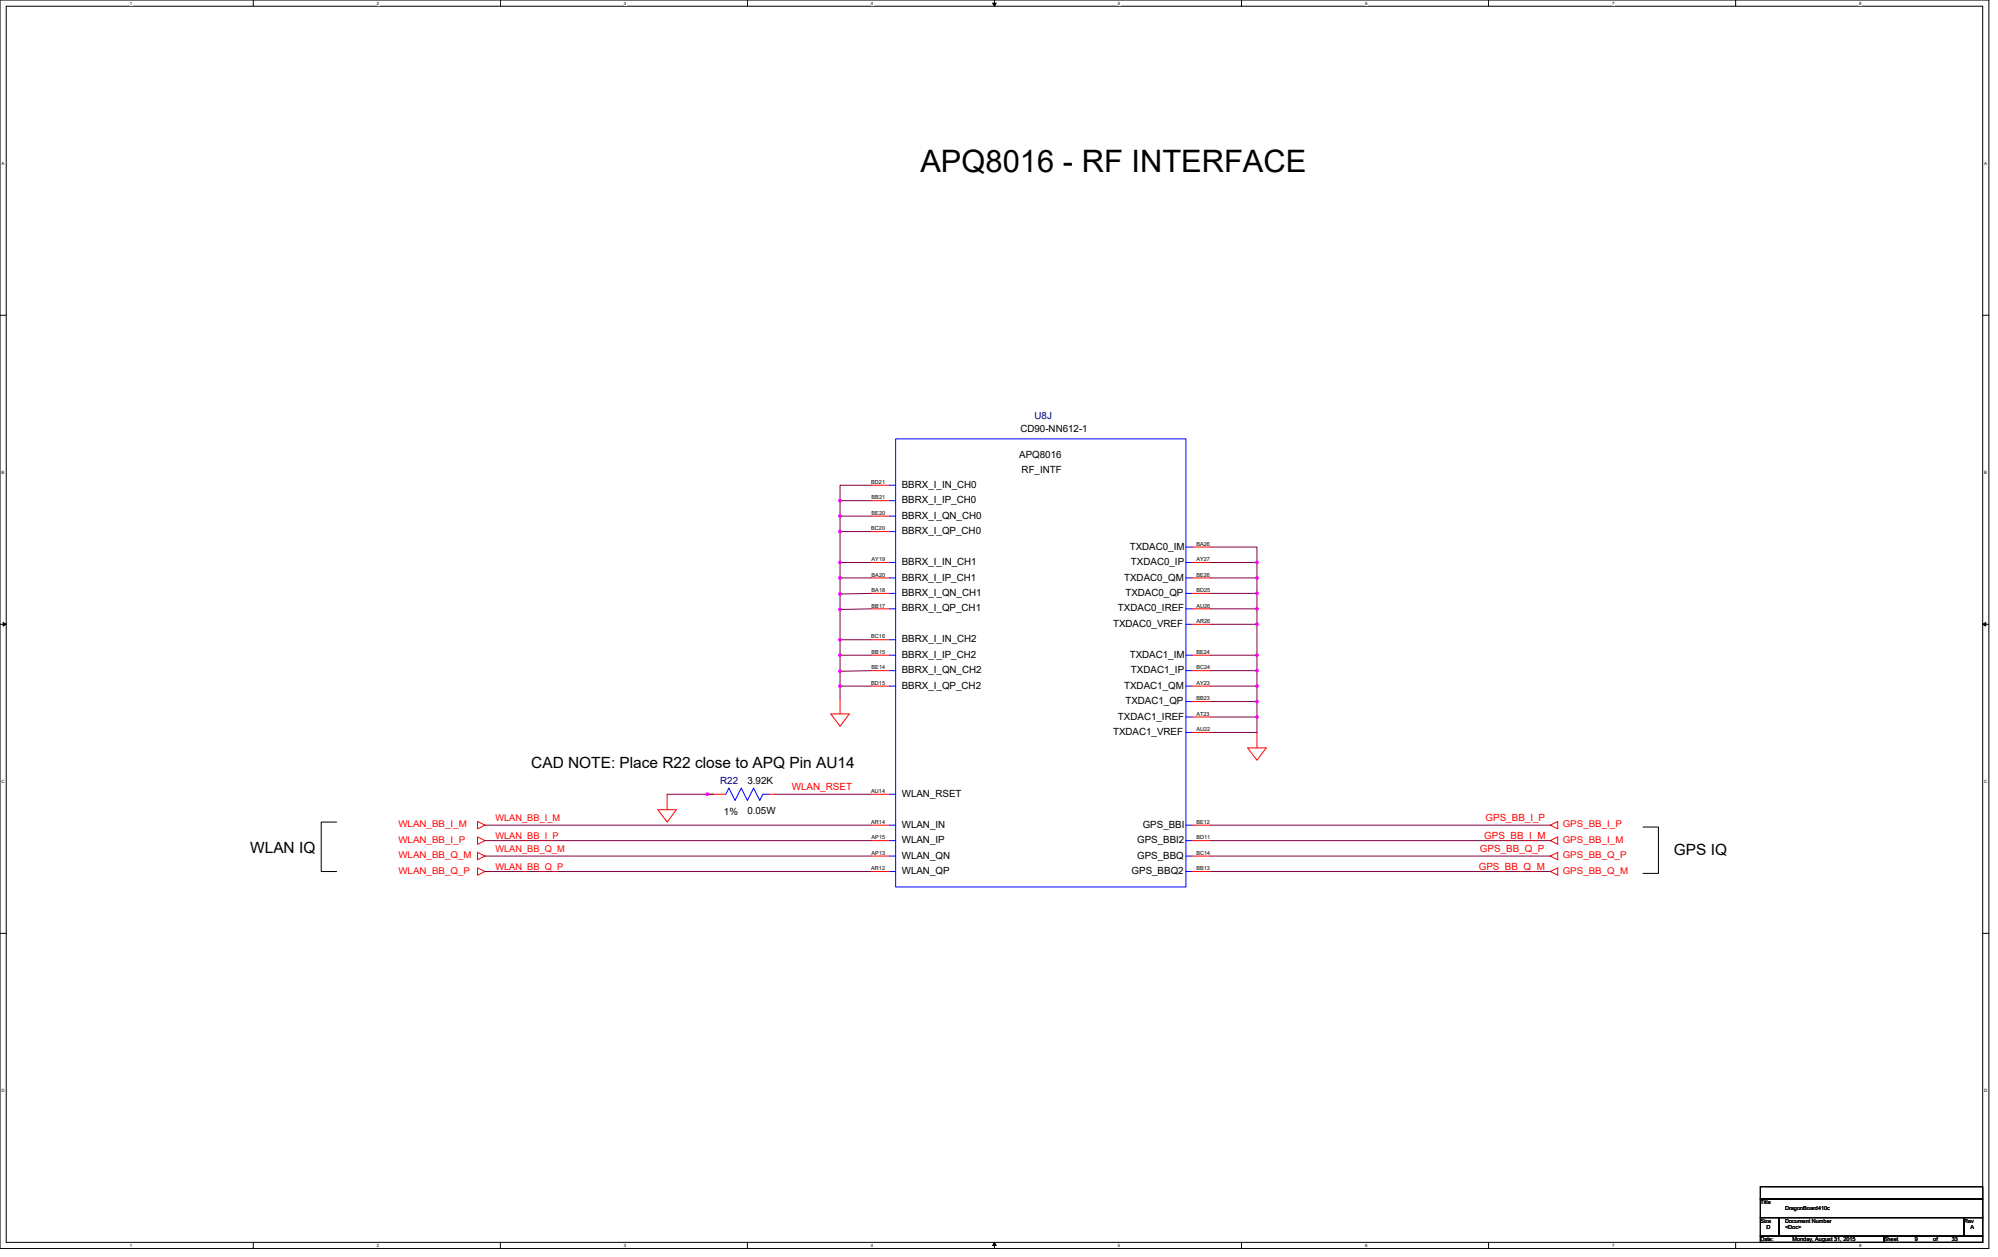
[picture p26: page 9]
WLAN IQ; GPS_BB_Q_P; GPS IQ; GPS_BB_Q_M; GPS_BB_I_P; GPS_BB_I_M; WLAN_BB_Q_P; WLAN_BB_Q_M; WLAN_BB_I_P; WLAN_BB_I_M; Monday, August 31, 2015; RF_INTF; APQ8016; BBRX_I_IN_CH0; BBRX_I_IN_CH1; BBRX_I_IN_CH2; BBRX_I_IP_CH0; BBRX_I_IP_CH1; BBRX_I_IP_CH2; BBRX_I_QN_CH0; BBRX_I_QN_CH1; BBRX_I_QN_CH2; BBRX_I_QP_CH0; BBRX_I_QP_CH1; BBRX_I_QP_CH2; BE12 GPS_BBI BD11 GPS_BBI2 BC14 GPS_BBQ GPS_BBQ2 BB13; BA26 TXDAC0_IM AY27 TXDAC0_IP; AU26 TXDAC0_IREF; BE26 TXDAC0_QM BD25 TXDAC0_QP; AR26 TXDAC0_VREF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

CAD NOTE: Place R22 close to APQ Pin AU14

# APQ8016 - PWR1

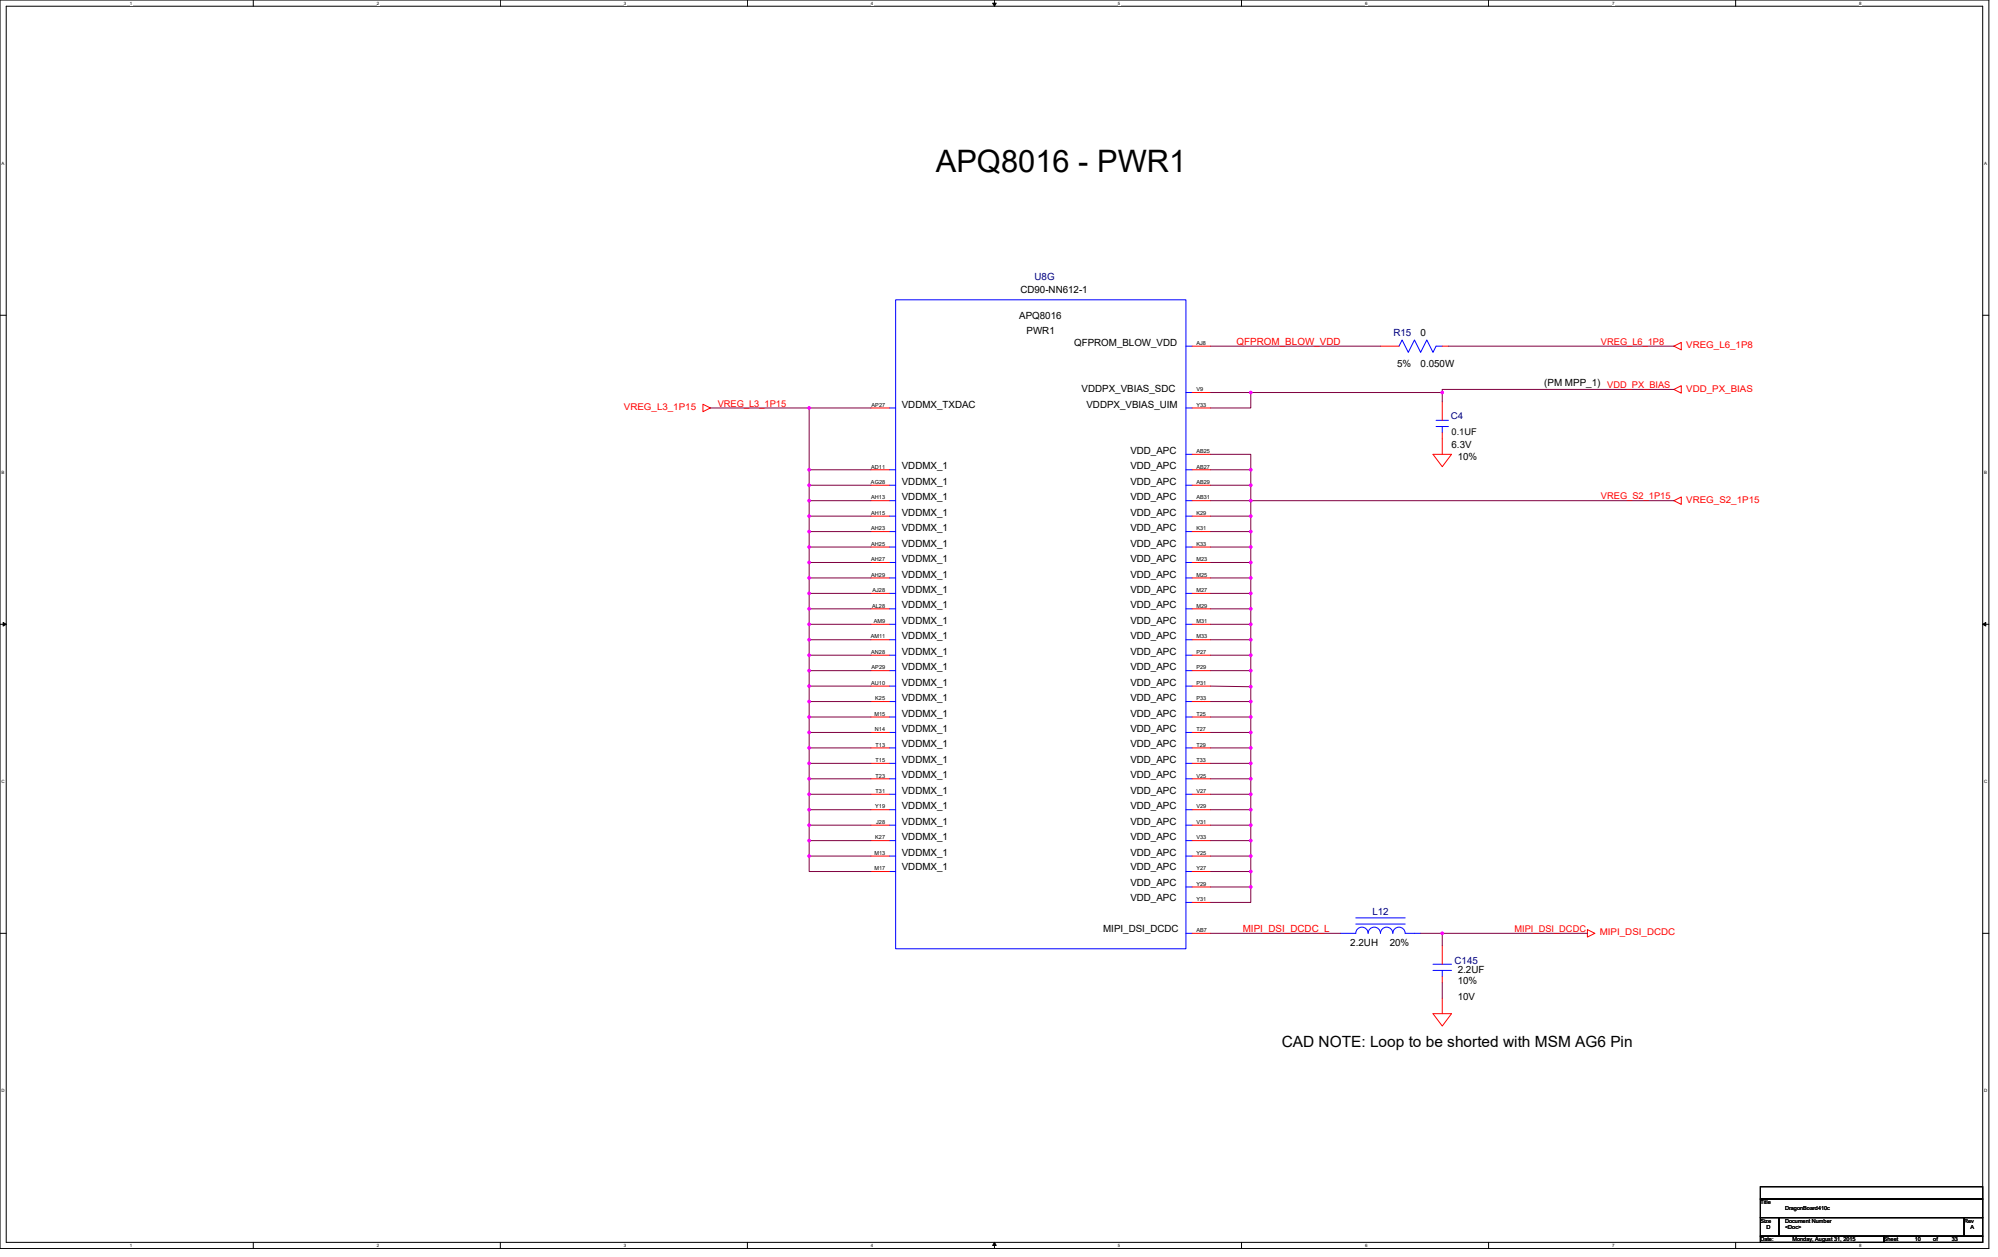
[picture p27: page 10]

CAD NOTE: Loop to be shorted with MSM AG6 Pin

# APQ8016 - PWR2

# APQ8016 - PWR3

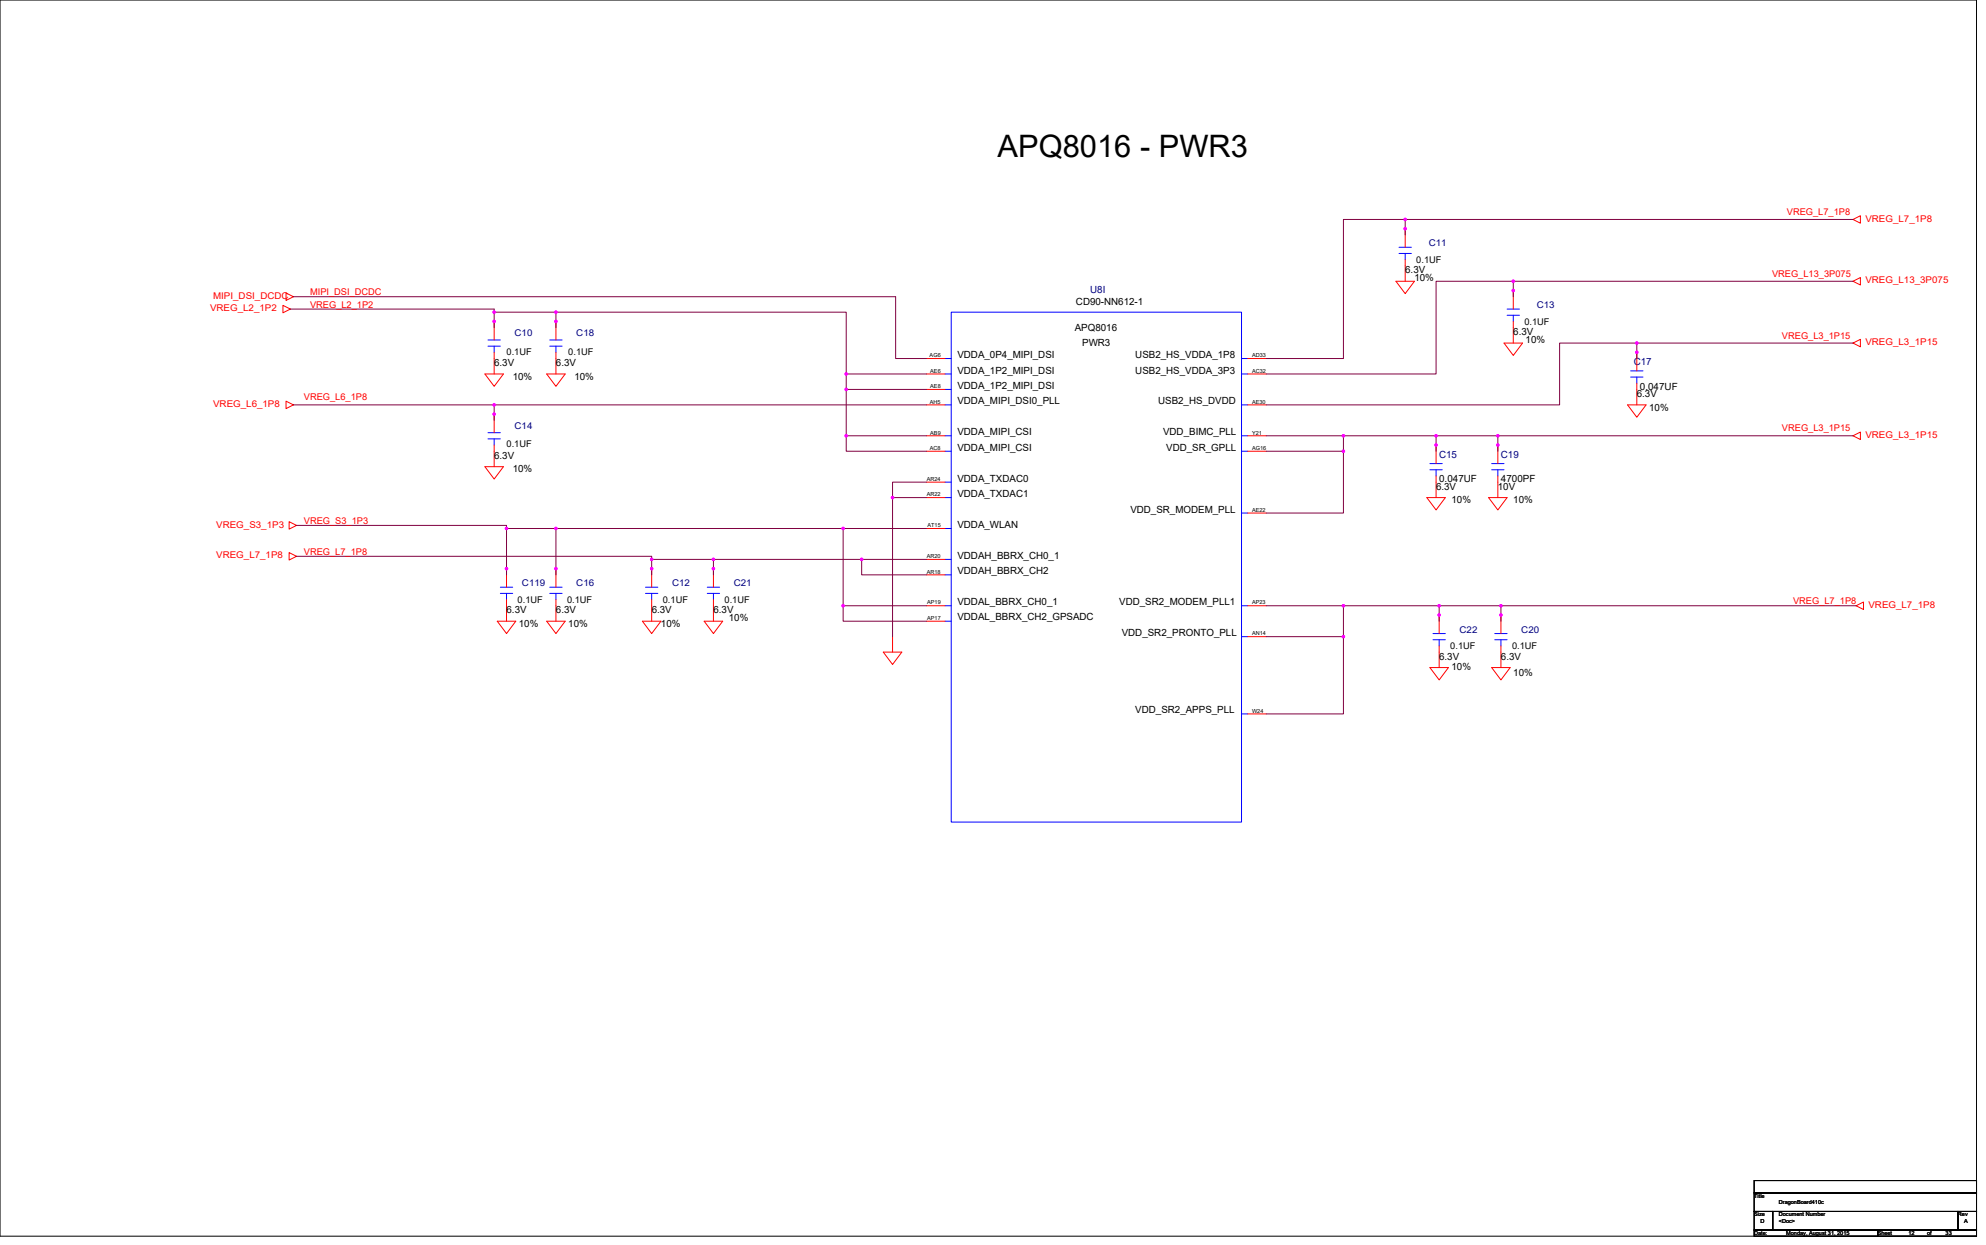
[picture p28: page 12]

# APQ8016 - GND

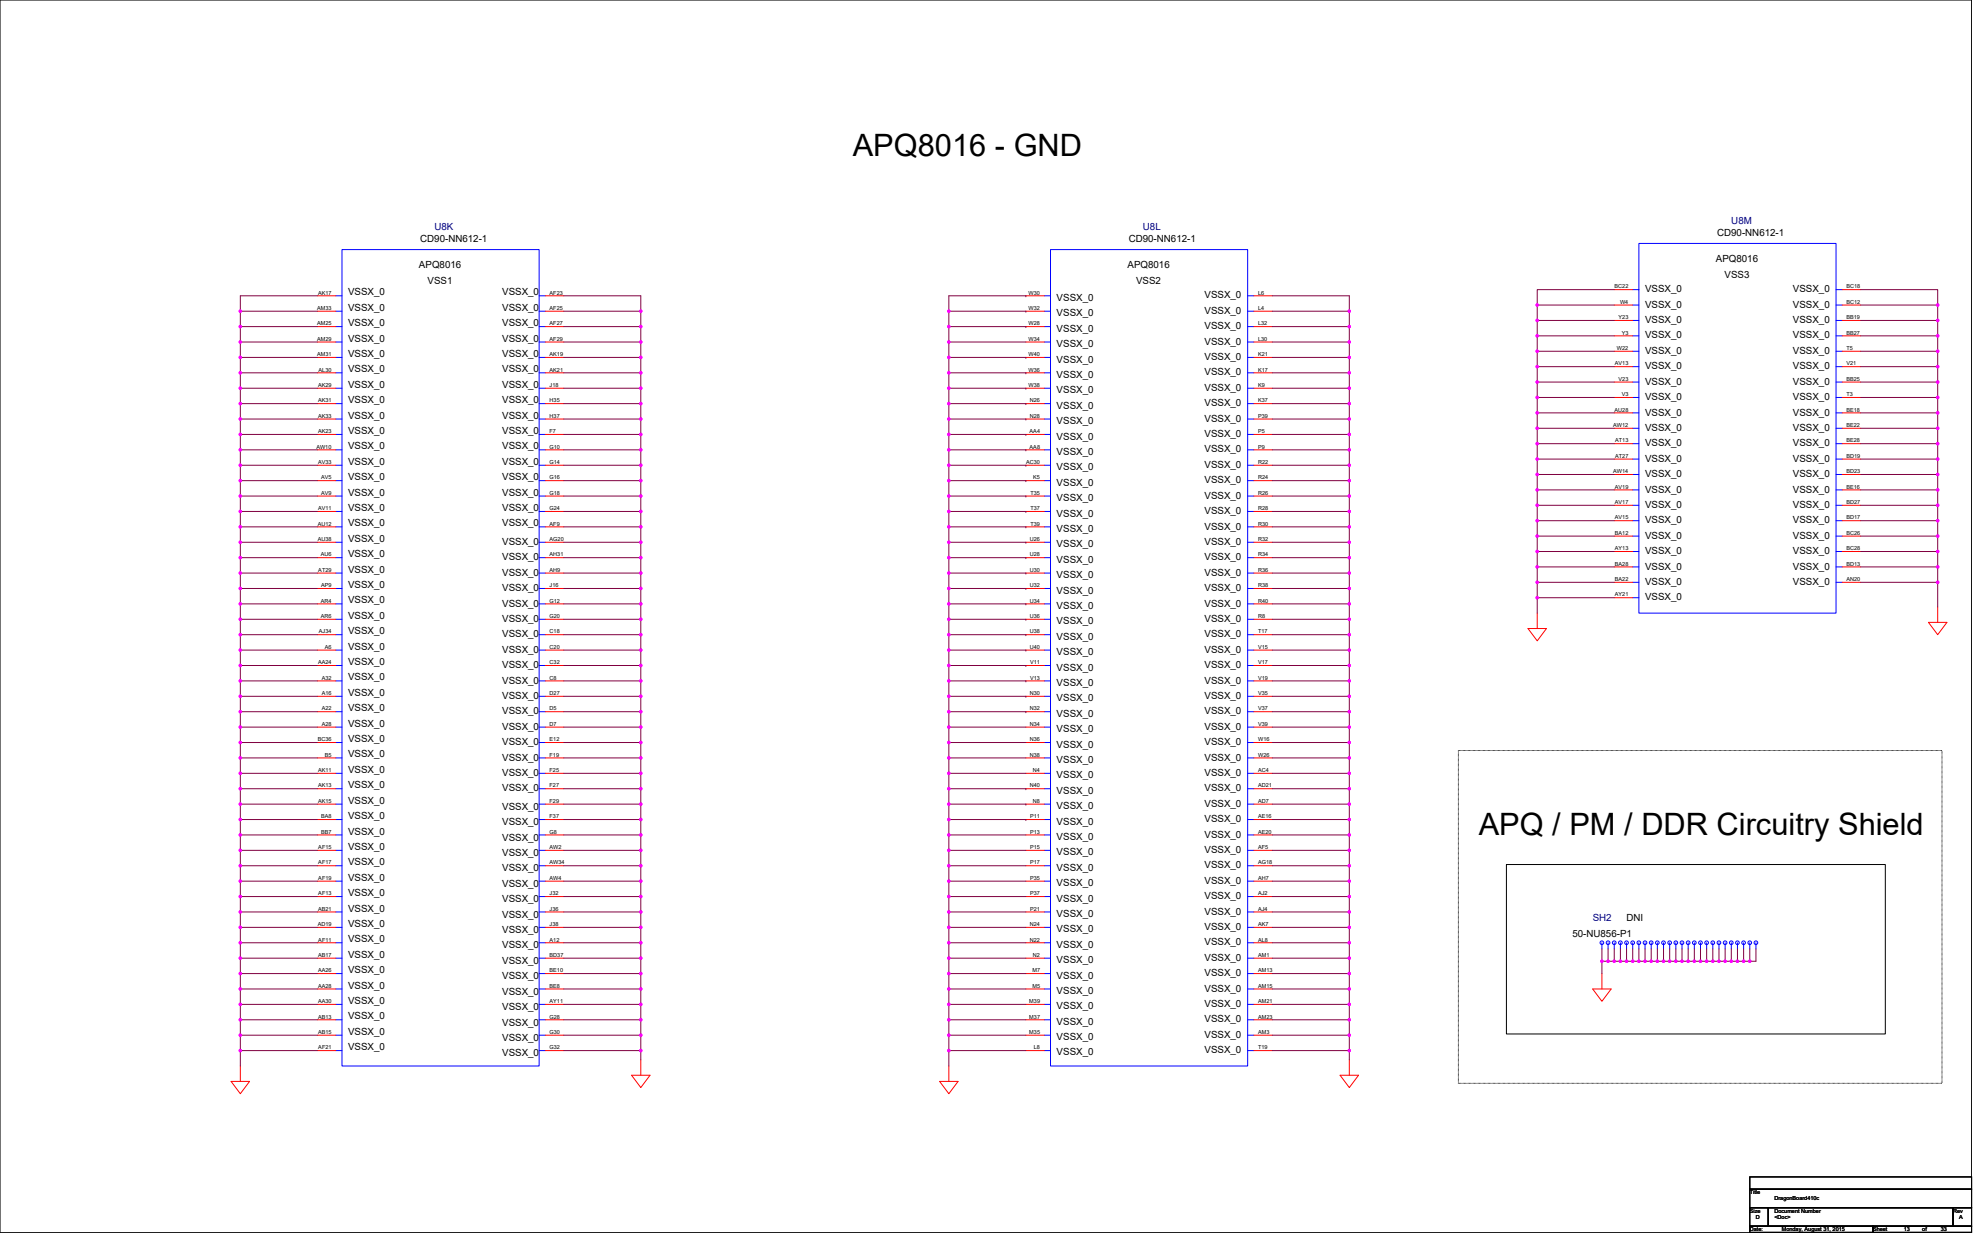
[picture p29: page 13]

APQ / PM / DDR Circuitry Shield

# APQ8016 BYPASS CAPACITORS

# PRE-BUCK - 5.0V

# EXTERNAL BUCK REGULATORS

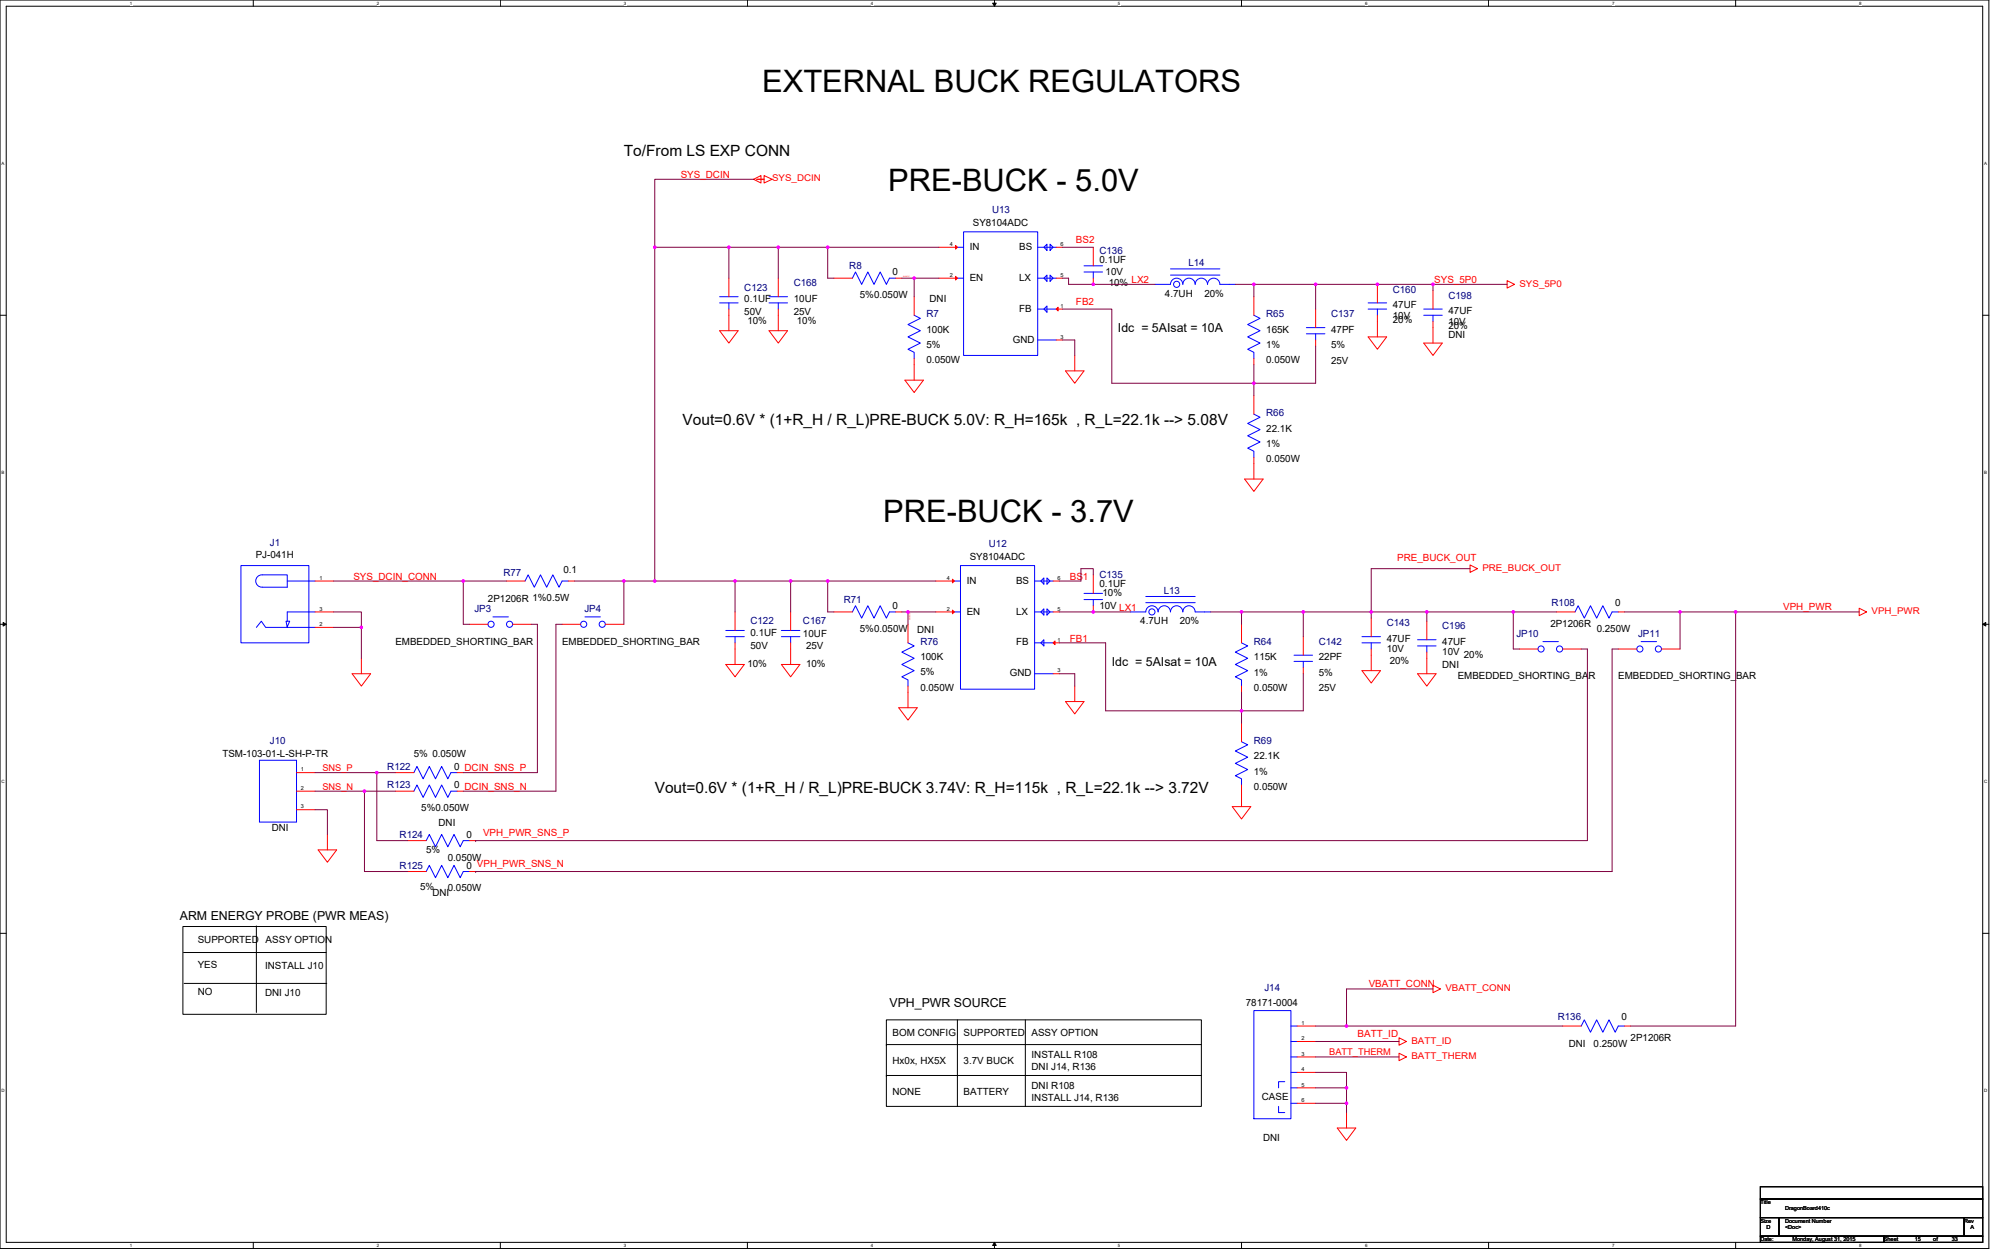
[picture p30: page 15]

To/From LS EXP CONN

ARM ENERGY PROBE (PWR MEAS)

SUPPORTED | ASSY OPTION

YES | INSTALL J10

NO | DNI J10

# PM8916 - CONTROL/CLOCKS

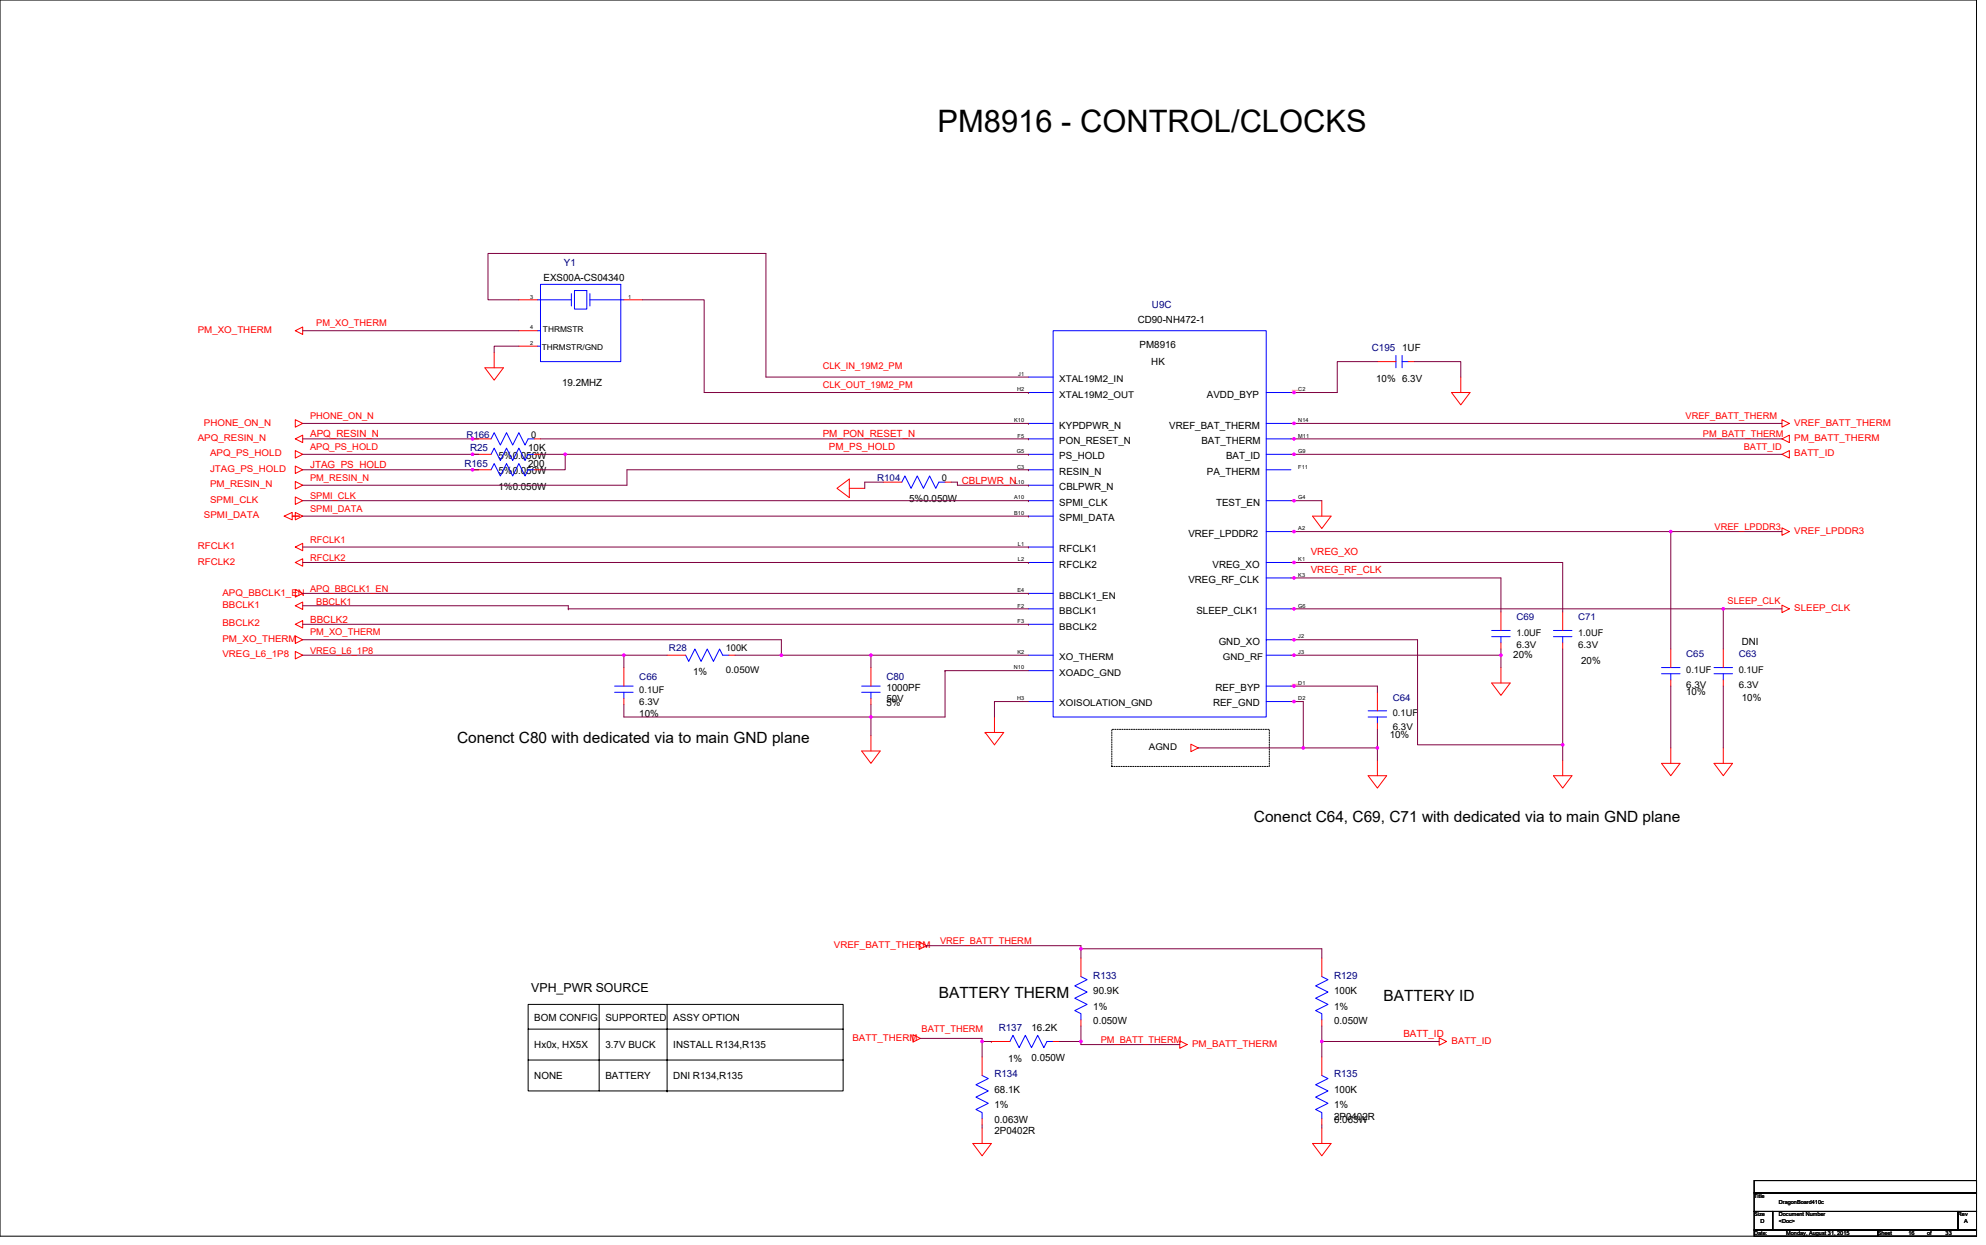
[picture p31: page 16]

Conenct C80 with dedicated via to main GND plane

Conenct C64, C69, C71 with dedicated via to main GND plane

BOM CONFIG | SUPPORTED | ASSY OPTION

Hx0x, HX5X | 3.7V BUCK | INSTALL R134,R135

NONE | BATTERY | DNI R134,R135

### VPH_PWR SOURCE

# PM8916 - CHARGER/GPIOS/MPPS

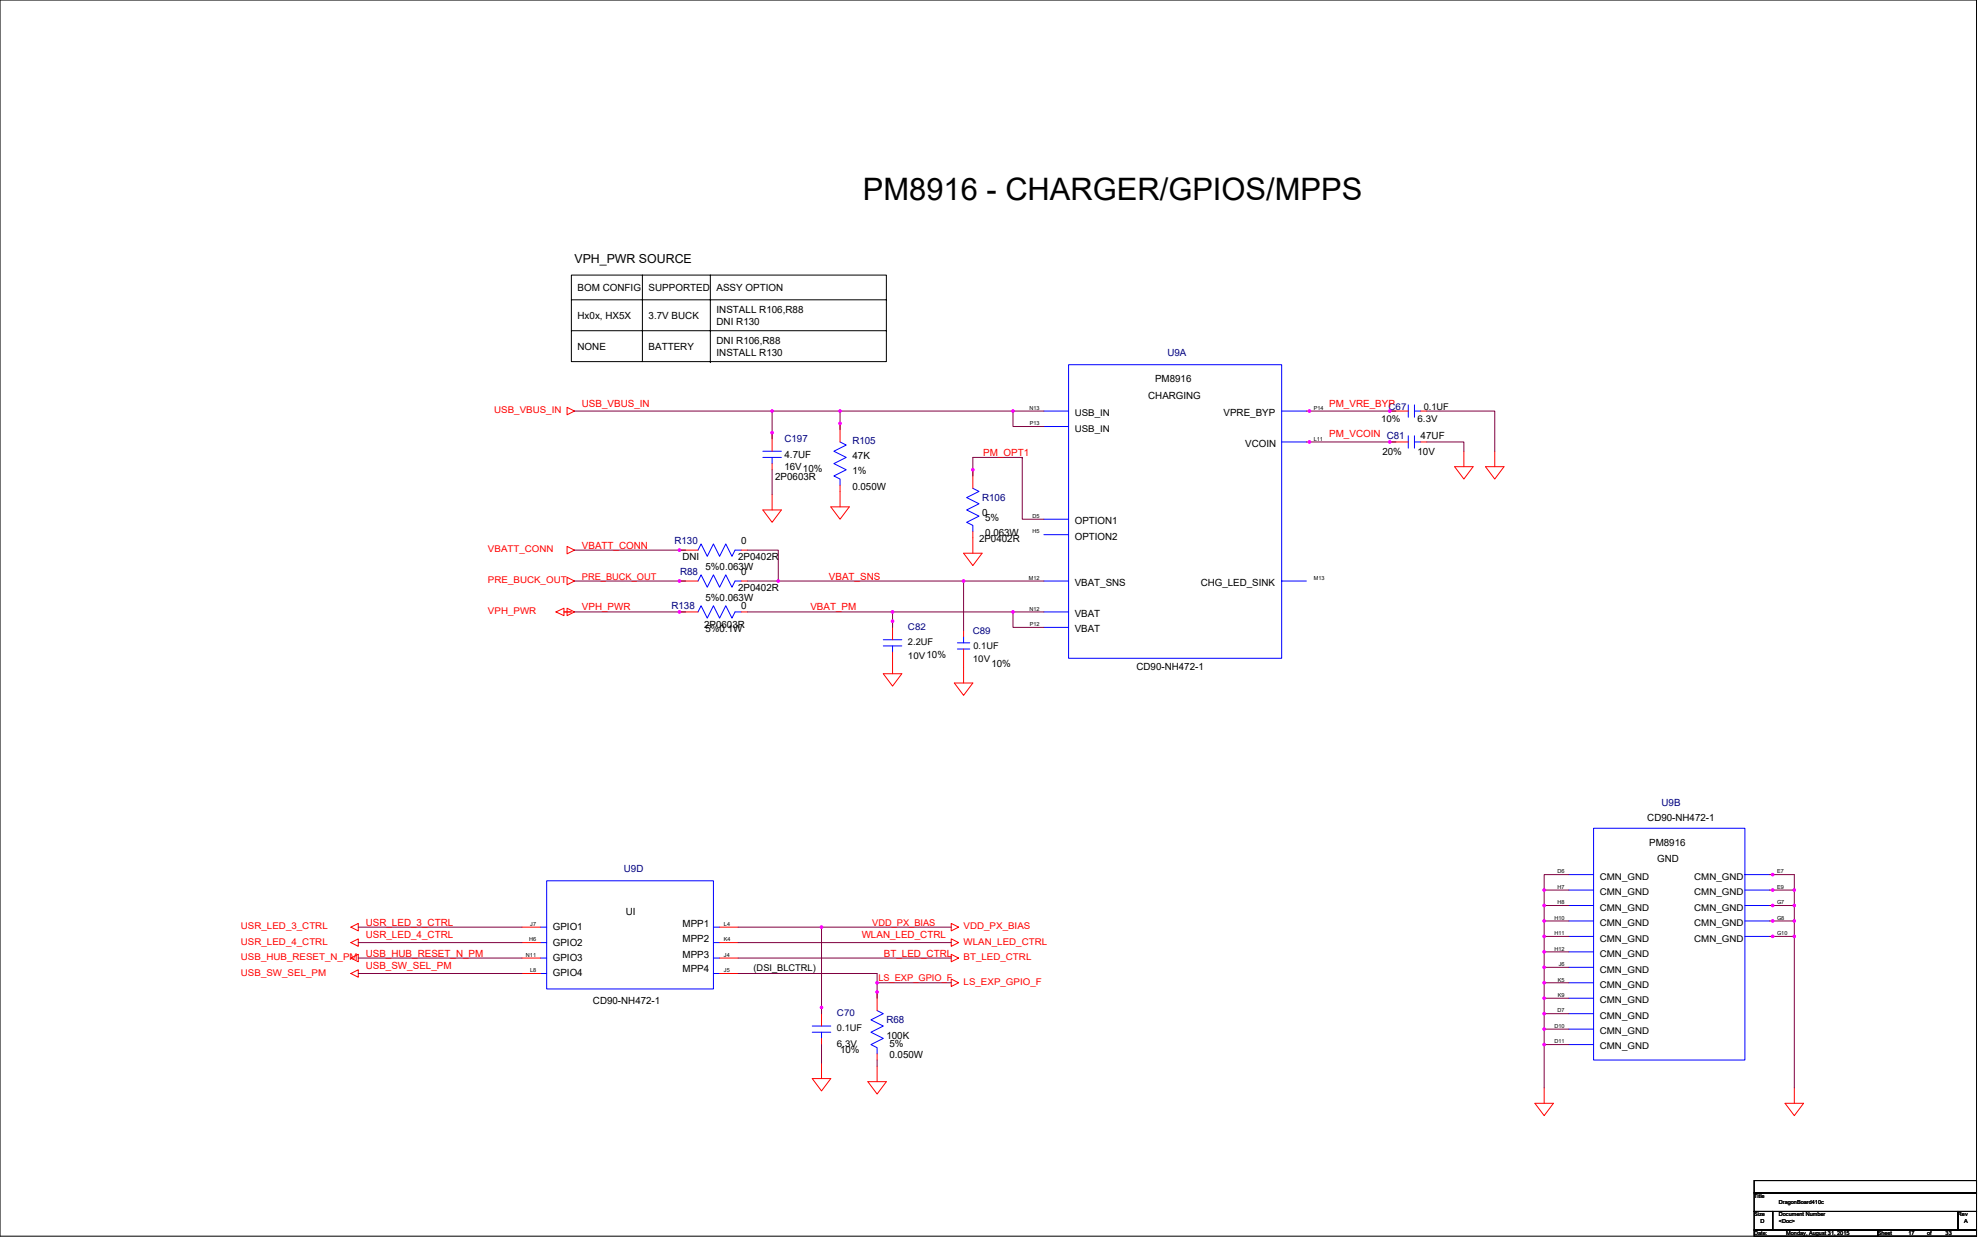
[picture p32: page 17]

BOM CONFIG | SUPPORTED | ASSY OPTION

Hx0x, HX5X | 3.7V BUCK | INSTALL R106,R88 DNI R130

NONE | BATTERY | DNI R106,R88 INSTALL R130

# PM8916 - SMPS
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

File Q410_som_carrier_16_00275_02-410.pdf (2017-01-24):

# PAGE DESCRIPTION

SCH. REV.

PCB REV.; DESCRIPTION; DATE; Q410 CARRIER; REFERENCE DESIGNATOR; I2C ADDRESS TABLE :; 7 BIT ADDRESS; USB2513BI-AEZG; MPU9250; PCA6416AHF,128; Q410 CARRIER SCHEMATICS; 22-June-2015; 22-Sept-2015; Title; Size; Project; Rev; Date:; Sheet; eInfochips#:; Designed eInfochips; COVER PAGE; Tuesday, September 22, 2015

MAJOR REVISION HISTORY :

PAGE 01 : COVER PAGE
PAGE 02 : BLOCK DIAGRAM
PAGE 03 : POWER SUPPLY TREE
PAGE 04 : MICRO SD AND JTAG
PAGE 05 : USB HUB
PAGE 06 : USB CONNECTORS
PAGE 07 : USB TO ETHERNET
PAGE 08 : LAN7500 POWER SUPPLY
PAGE 09 : MIPI DSI DISPLAY
PAGE 10 : MIPI CAMERA
PAGE 11 : HEADSET,MIC & SPEAKER
PAGE 12 : LED AND SWICHES
PAGE 13 : GPS-WGR7640
PAGE 14 : GYROSCOPE & ACCELEROMETER
PAGE 15 : INPUT SUPPLY AND LDO
PAGE 16 : POWER SUPPLY
PAGE 17 : BOOT CONFIGURATION AND DEBUG
PAGE 18 : I/O EXPANDER
PAGE 19 : EXPANSION CONNECTOR
PAGE 20 : REVISION HISTORY

PCB LAYER STACK-UP DETAILS :

PCB MECHANICAL DETAILS :

1. PCB SIZE: 72 mm X 100 mm
2. PCB MATERIAL: FR4
3. NUMBER OF LAYERS: 8
4. IMPEDANCE CONTROL: YES

NOTES, UNLESS OTHERWISE SPECIFIED :

1. RESISTANCE VALUES ARE IN OHMS.
2. CAPACITANCE VALUES ARE IN MICROFARADS.
3. PARTS NOT INSTALLED ARE INDICATED WITH 'DNP'.
4. SIGNAL NET NAMES WITH "_N" SUFFIX, ARE ACTIVE LOW SIGNALS.

THE CONTENTS OF THIS DOCUMENT ARE PROPRIETARY TO EINFOCHIPS. ANY CONTENTS OF THIS DOCUMENT SHALL NOT BE
DISCLOSED, DISSEMINATED, COPIED OR USED EXCEPT FOR PURPOSES EXPRESSLY AUTHORIZED IN WRITING BY EINFOCHIPS.
Copyrights 2015 eInfochips Ltd.
All Rights Reserved.

# BLOCK DIAGRAM

Title; Project; Designed eInfochips; BLOCK DIAGRAM; Friday, September 18, 2015; Q410 CARRIER

# POWER SUPPLY DISTRIBUTION

Designed eInfochips; Friday, September 18, 2015

Project
Q410 CARRIER
Title
POWER SUPPLY DISTRIBUTION

# MEMORY - Micro SD CONNECTOR


CAD NOTE: PLACE THESE CAPACITORS CLOSE TO VDD PIN

CAD NOTE: PLACE THIS ESD CLOSE TO CD_SWA PIN

NOTE: SEPARATE ESD IS REQUIRED FOR SD_CARD_DET_N.

CAD NOTE: PLACE ESD CLOSE TO SD CONNECTOR

Connection beween Pin9(CD)
and Pin10(GND) will be open.
It meanse SW is OFF

and Pin10(GND) will be closed.
It meanse SW is ON

Design Note:Faulty SD card or hot swap will cause short circuit between VDD and ground, so an external LDO with short
circuit protection should be used to power SD card.

NOTE: JTAG (RTCK) PIN IS NOT AVAILABLE IN APQ8016.

# USB HUB

### FORCE DSI SELECTION TO USB HOST MODE


Layout: 90 Ohm Differential Pairs

OPTION TO BYPASS LOAD SWITCH

CAD NOTE: PLACE THESE CAPACITORS AS CLOSER TO RESPECTIVE IC'S PIN

CAD NOTE: PLACE THESE CAPACITORS AS CLOSER TO THE CRYSTAL

0 Internal Defaults (Self Powered)

Internal Default (Bus Power)

# USB - CONNECTORS

# USB2.0 - DEVICE


CAD NOTE: 90 Ohm Differential Pairs

CAD NOTE: PLACE THIS ESD CLOSE TO J3 (OTG) CONNECTOR.

ON - USB DEVICE MODE

OFF - USB HOST MODE

NOTE: USB Device Detection

CAD NOTE: PLACE THIS ESD CLOSE TO CONNECTOR J4A

Layout: 90 Ohm Differential Pairs

# USB TO ETHRENET

CAD NOTE: PLACE R42 (12k) CLOSE TO USBRBAIS PIN.


CAD NOTE: PLACE C36 AND C37 CAPACITORS NEAREST TO THE OSCILLATOR

CAD NOTE: PLACE THESE CAPACITORS NEAREST TO CONNECTOR (J4B).

Layout: 100 Ohm Differential Pairs

CAD NOTE: C38-C45 ARE OPTIONAL. IN AN EMI
ENVIRONMENT,POPULATE THESE CAPACITORS.

# LAN 7500 - POWER SUPPLY


LAN 7500 - POWER SUPPLY FILTER

# MIPI DSI DISPLAY

# DISPLAY CONNECTOR


Layout: 100 Ohm Differential Pairs

# MIPI CAMERA

PRIMARY CAMERA | SECONDARY CAMERA


### NOTE : FOR DEFUALT INSTALLATION MOUNT R102

# MIC,HEADSET & SPEAKER


CAD NOTE : Place L and C near the headset jack ground

and star route their traces in layout.

NOTE : Ferrite beads are required to improve FM performance.
Place them close to the headset.

NOTE: Place FB19, FB20, C108 and C109
close to headset jack connector.

NOTE: Place ESD11& ESD12 close to
SPEAKER J25 connector.

NOTE: Place ESD2 & ESD3 close to

NOTE: Place ESD16 close to

CAD NOTE:
Route two traces as differential Signals.

# LEDS

VPH PWR INDICATOR LED | VPH_PWR


# GPS-WGR7640
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



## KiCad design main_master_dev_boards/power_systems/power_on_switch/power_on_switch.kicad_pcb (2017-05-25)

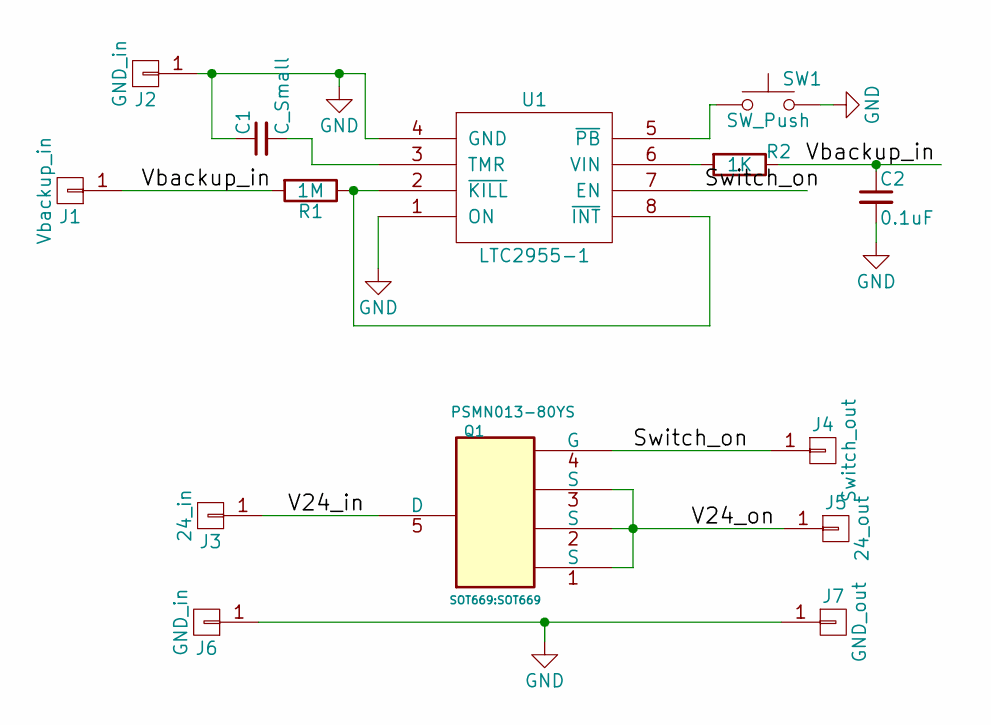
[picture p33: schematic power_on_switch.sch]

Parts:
C1: C_Small; C_0805_HandSoldering
C2: 0.1uF; C_0805_HandSoldering
J1: Vbackup_in; pinhead-01x01_3x1
J2, J6: GND_in; pinhead-01x01_3x1_square
J3: 24_in; pinhead-01x01_3x1
J4: Switch_out; pinhead-01x01_3x1
J5: 24_out; pinhead-01x01_3x1
J7: GND_out; pinhead-01x01_3x1_square
Q1: PSMN013-80YS; SOT669
R1: 1M; R_0805_HandSoldering
R2: 1K; R_0805_HandSoldering
SW1: SW_Push; microclasp_2
U1: LTC2955-1; TSOT-23-8

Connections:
/Switch_on: J4.1, Q1.4 (G), U1.7 (EN)
/V24_in: J3.1, Q1.5 (D)
/V24_on: J5.1, Q1.1 (S), Q1.2 (S), Q1.3 (S)
/Vbackup_in: C2.1, J1.1, R1.2, R2.1
GND: C1.1, C2.2, J2.1, J6.1, J7.1, SW1.2, U1.1 (ON), U1.4 (GND)
unnamed: C1.2, U1.3 (TMR)
unnamed: R1.1, U1.2 (~KILL), U1.8 (~INT)
unnamed: R2.2, U1.6 (VIN)
unnamed: SW1.1, U1.5 (~PB)

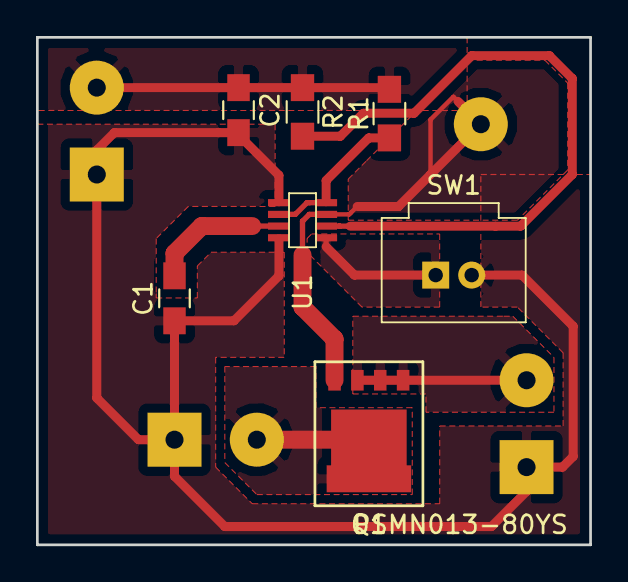
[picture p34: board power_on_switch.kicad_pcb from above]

Board: 2 copper layers, 30.7 x 28.2 mm, 14 parts (0 on the bottom side), 9 nets.

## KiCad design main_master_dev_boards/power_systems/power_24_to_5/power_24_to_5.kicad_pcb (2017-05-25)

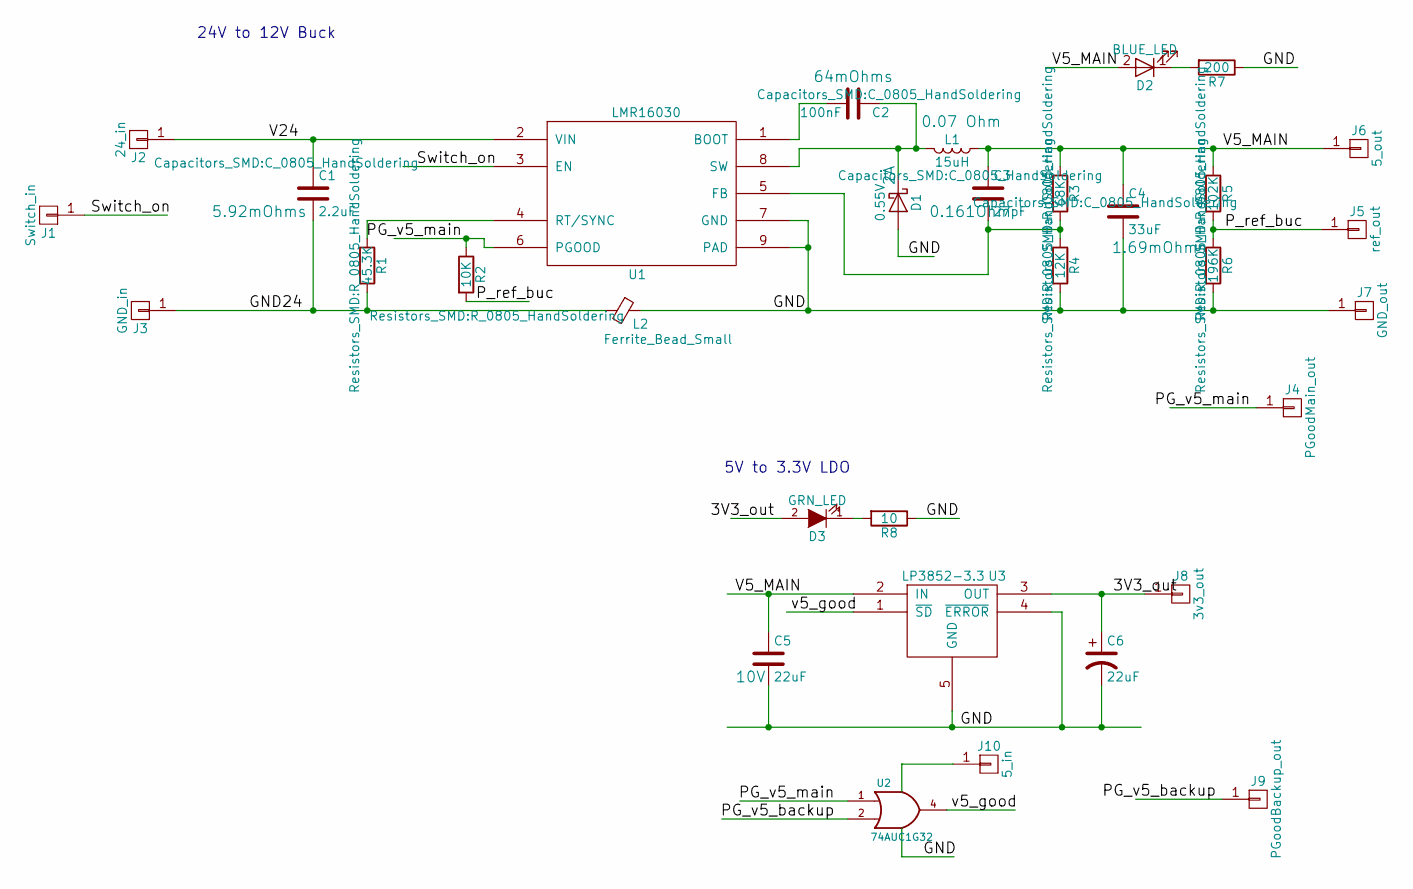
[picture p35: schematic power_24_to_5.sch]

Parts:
C1: 2.2uF; C_0805_HandSoldering
C2: 100nF; C_0805_HandSoldering
C3: 27pF; C_0805_HandSoldering
C4: 33uF; C_0805_HandSoldering
C5: 22uF; C_0805_HandSoldering; Voltage 10V
C6: 22uF; C_0805_HandSoldering
D1: 0.55V; D_SOD-123
D2: BLUE_LED; LED_0603
D3: GRN_LED; LED_0603
J1: Switch_in; pinhead-01x01_3x1
J2: 24_in; pinhead-01x01_3x1
J3: GND_in; pinhead-01x01_3x1_square
J4: PGoodMain_out; pinhead-01x01_3x1
J5: ref_out; pinhead-01x01_3x1
J6: 5_out; pinhead-01x01_3x1
J7: GND_out; pinhead-01x01_3x1_square
J8: 3v3_out; pinhead-01x01_3x1
J9: PGoodBackup_out; pinhead-01x01_3x1
J10: 5_in; pinhead-01x01_3x1
L1: 15uH; Bourns-8040
L2: Ferrite_Bead_Small; C_0805_HandSoldering
R1: 45.3K; R_0805_HandSoldering
R2: 10K; R_0805_HandSoldering
R3: 68K; R_0805_HandSoldering
R4: 12K; R_0805_HandSoldering
R5: 102K; R_0805_HandSoldering
R6: 196K; R_0805_HandSoldering
R7: 200; R_0805_HandSoldering
R8: 10; R_0805_HandSoldering
U1: LMR16030; HSOIC-8-1EP_Pitch1.27mm_noVias
U2: 74AUC1G32; SOT-23-5_HandSoldering
U3: LP3852-3.3; SOT-223

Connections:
/3V3_out: C6.1, D3.2 (A), J8.1, U3.3 (OUT)
/GND24: C1.2, J3.1, L2.2, R1.2
/PG_v5_backup: J9.1, U2.2
/PG_v5_main: J4.1, R2.1, U1.6 (PGOOD), U2.1
/P_ref_buc: J5.1, R2.2, R5.2, R6.1
/Switch_on: J1.1, U1.3 (EN)
/V5_MAIN: C3.1, C4.1, C5.1, D2.2 (A), J6.1, L1.1, R3.1, R5.1, U3.2 (IN)
/V24: C1.1, J2.1, U1.2 (VIN)
/v5_good: U2.4, U3.1 (~SD)
GND: C4.2, C5.2, C6.2, D1.2 (A), J7.1, L2.1, R4.2, R6.2, R7.1, R8.1, U1.7 (GND), U1.9 (PAD), U2.3 (GND), U3.4 (~ERROR), U3.5 (GND)
unnamed: C2.1, D1.1 (K), L1.2, U1.8 (SW)
unnamed: C2.2, U1.1 (BOOT)
unnamed: C3.2, R3.2, R4.1, U1.5 (FB)
unnamed: D2.1 (K), R7.2
unnamed: D3.1 (K), R8.2
unnamed: R1.1, U1.4 (RT/SYNC)
VCC: J10.1, U2.5 (VCC)

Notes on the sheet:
24V to 12V Buck
5V to 3.3V LDO

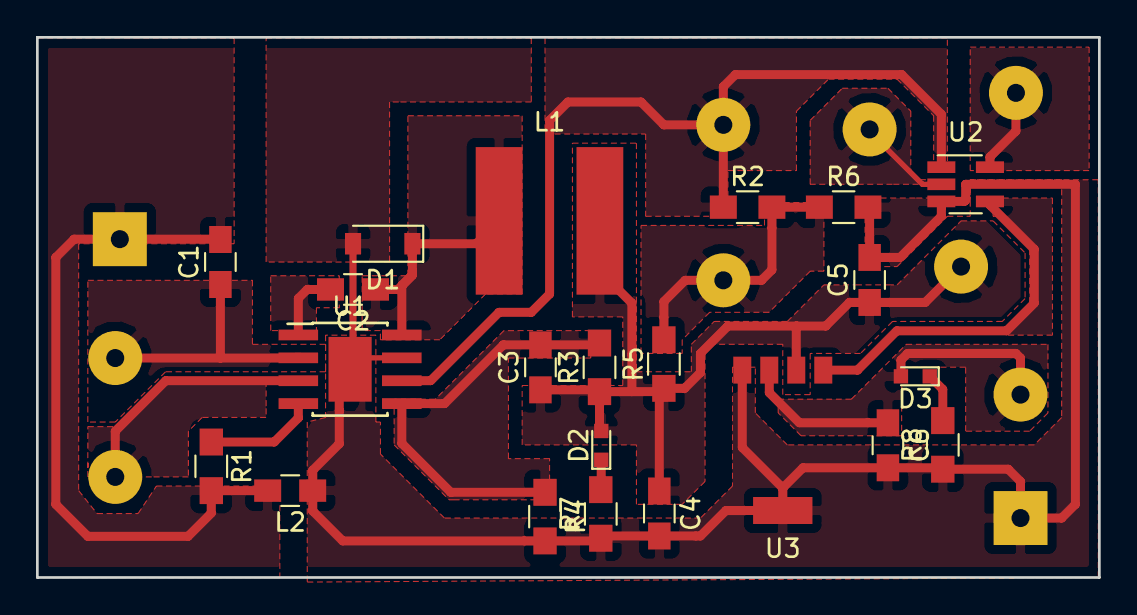
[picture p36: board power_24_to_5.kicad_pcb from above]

Board: 2 copper layers, 59.0 x 30.0 mm, 32 parts (0 on the bottom side), 17 nets.

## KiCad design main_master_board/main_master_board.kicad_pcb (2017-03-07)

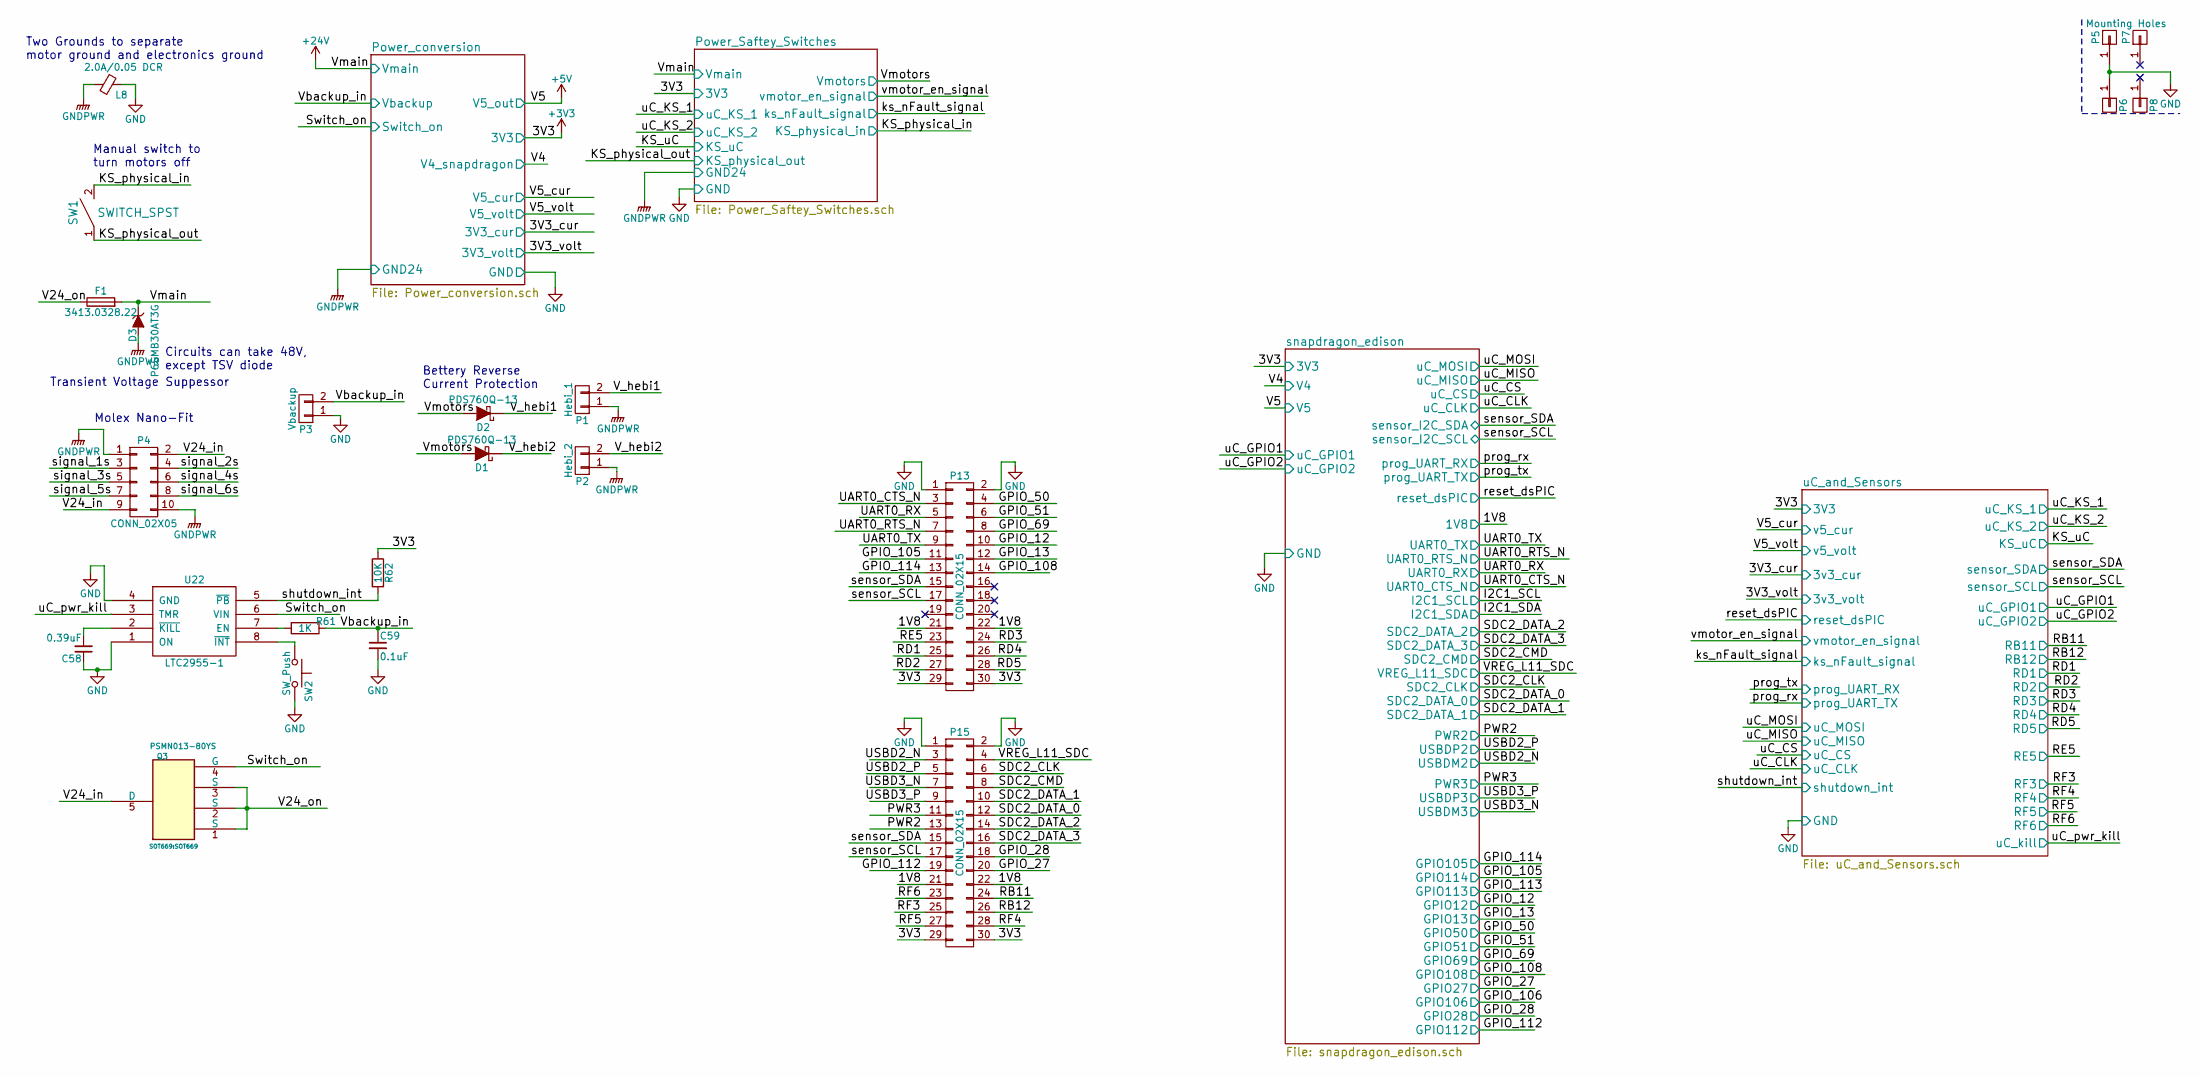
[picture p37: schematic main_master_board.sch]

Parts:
C58: 0.39uF; C_0402
C59: 0.1uF; C_0402
D1, D2: PDS760Q-13; PowerDI
D3: P6SMB30AT3G; SMB_Standard
F1: 3413.0328.22; dp_devices-C1206
L8: 2.0A/0.05 DCR; dp_devices-C603
P1: Hebi_1; Molex_MiniFit-JR-5556-02A_2x01x4.20mm_Straight
P2: Hebi_2; Molex_MiniFit-JR-5556-02A_2x01x4.20mm_Straight
P3: Vbackup; microclasp_2
P4: CONN_02X05; Molex_NanoFit_2x05x2.50mm_Straight
P5, P6, P7, P8: Mounting Holes; MountingHole_3.2mm_M3_Pad
P13, P15: CONN_02X15; DF40HC(3.5)-30DS-0.4V(51)
Q3: PSMN013-80YS; SOT669
R61: 1K; R_0402
R62: 10K; R_0402
SW1: SWITCH_SPST; microclasp_2
SW2: SW_Push; microclasp_2
U22: LTC2955-1; TSOT-23-8

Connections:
+1V8: P13.21, P13.22, P15.21, P15.22; also elsewhere on the board
+3V3: P13.29, P13.30, P15.29, P15.30, R62.1; also elsewhere on the board
+24V: D3.1 (K), F1.2; also elsewhere on the board
/GPIO_12: P13.10; also elsewhere on the board
/GPIO_13: P13.12; also elsewhere on the board
/GPIO_27: P15.20; also elsewhere on the board
/GPIO_28: P15.18; also elsewhere on the board
/GPIO_50: P13.4; also elsewhere on the board
/GPIO_51: P13.6; also elsewhere on the board
/GPIO_69: P13.8; also elsewhere on the board
/GPIO_105: P13.11; also elsewhere on the board
/GPIO_108: P13.14; also elsewhere on the board
/GPIO_112: P15.19; also elsewhere on the board
/GPIO_114: P13.13; also elsewhere on the board
/KS_physical_in: SW1.2; also elsewhere on the board
/KS_physical_out: SW1.1; also elsewhere on the board
/PWR2: P15.13; also elsewhere on the board
/PWR3: P15.11; also elsewhere on the board
/RB11: P15.24; also elsewhere on the board
/RB12: P15.26; also elsewhere on the board
/RD1: P13.25; also elsewhere on the board
/RD2: P13.27; also elsewhere on the board
/RD3: P13.24; also elsewhere on the board
/RD4: P13.26; also elsewhere on the board
/RD5: P13.28; also elsewhere on the board
/RE5: P13.23; also elsewhere on the board
/RF3: P15.25; also elsewhere on the board
/RF4: P15.28; also elsewhere on the board
/RF5: P15.27; also elsewhere on the board
/RF6: P15.23; also elsewhere on the board
/SDC2_CLK: P15.6; also elsewhere on the board
/SDC2_CMD: P15.8; also elsewhere on the board
/SDC2_DATA_0: P15.12; also elsewhere on the board
/SDC2_DATA_1: P15.10; also elsewhere on the board
/SDC2_DATA_2: P15.14; also elsewhere on the board
/SDC2_DATA_3: P15.16; also elsewhere on the board
/Switch_on: Q3.4 (G), U22.6 (VIN); also elsewhere on the board
/UART0_CTS_N: P13.3; also elsewhere on the board
/UART0_RTS_N: P13.7; also elsewhere on the board
/UART0_RX: P13.5; also elsewhere on the board
/UART0_TX: P13.9; also elsewhere on the board
/USBD2_N: P15.3; also elsewhere on the board
/USBD2_P: P15.5; also elsewhere on the board
/USBD3_N: P15.7; also elsewhere on the board
/USBD3_P: P15.9; also elsewhere on the board
/V24_in: P4.2, P4.9, Q3.5 (D)
/V24_on: F1.1, Q3.1 (S), Q3.2 (S), Q3.3 (S)
/VREG_L11_SDC: P15.4; also elsewhere on the board
/V_hebi1: D2.1 (K), P1.2
/V_hebi2: D1.1 (K), P2.2
/Vbackup_in: C59.1, P3.2, R61.1; also elsewhere on the board
/Vmotors: D1.2 (A), D2.2 (A); also elsewhere on the board
/sensor_SCL: P13.17, P15.17; also elsewhere on the board
/sensor_SDA: P13.15, P15.15; also elsewhere on the board
/shutdown_int: R62.2, U22.5 (~PB); also elsewhere on the board
/signal_1s: P4.3
/signal_2s: P4.4
/signal_3s: P4.5
/signal_4s: P4.6
/signal_5s: P4.7
/signal_6s: P4.8
/uC_pwr_kill: U22.3 (TMR); also elsewhere on the board
GND: C58.1, C59.2, L8.1, P3.1, P5.1, P6.1, P13.1, P13.2, P15.1, P15.2, SW2.2, U22.1 (ON), U22.4 (GND); also elsewhere on the board
GNDPWR: D3.2 (A), L8.2, P1.1, P2.1, P4.1, P4.10; also elsewhere on the board
unnamed: C58.2, U22.2 (~KILL)
unnamed: R61.2, U22.7 (EN)
unnamed: SW2.1, U22.8 (~INT)

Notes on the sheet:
Two Grounds to separate motor ground and electronics ground
Molex Nano-Fit
Bettery Reverse Current Protection
Manual switch to turn motors off
Transient Voltage Suppessor
Circuits can take 48V, except TSV diode

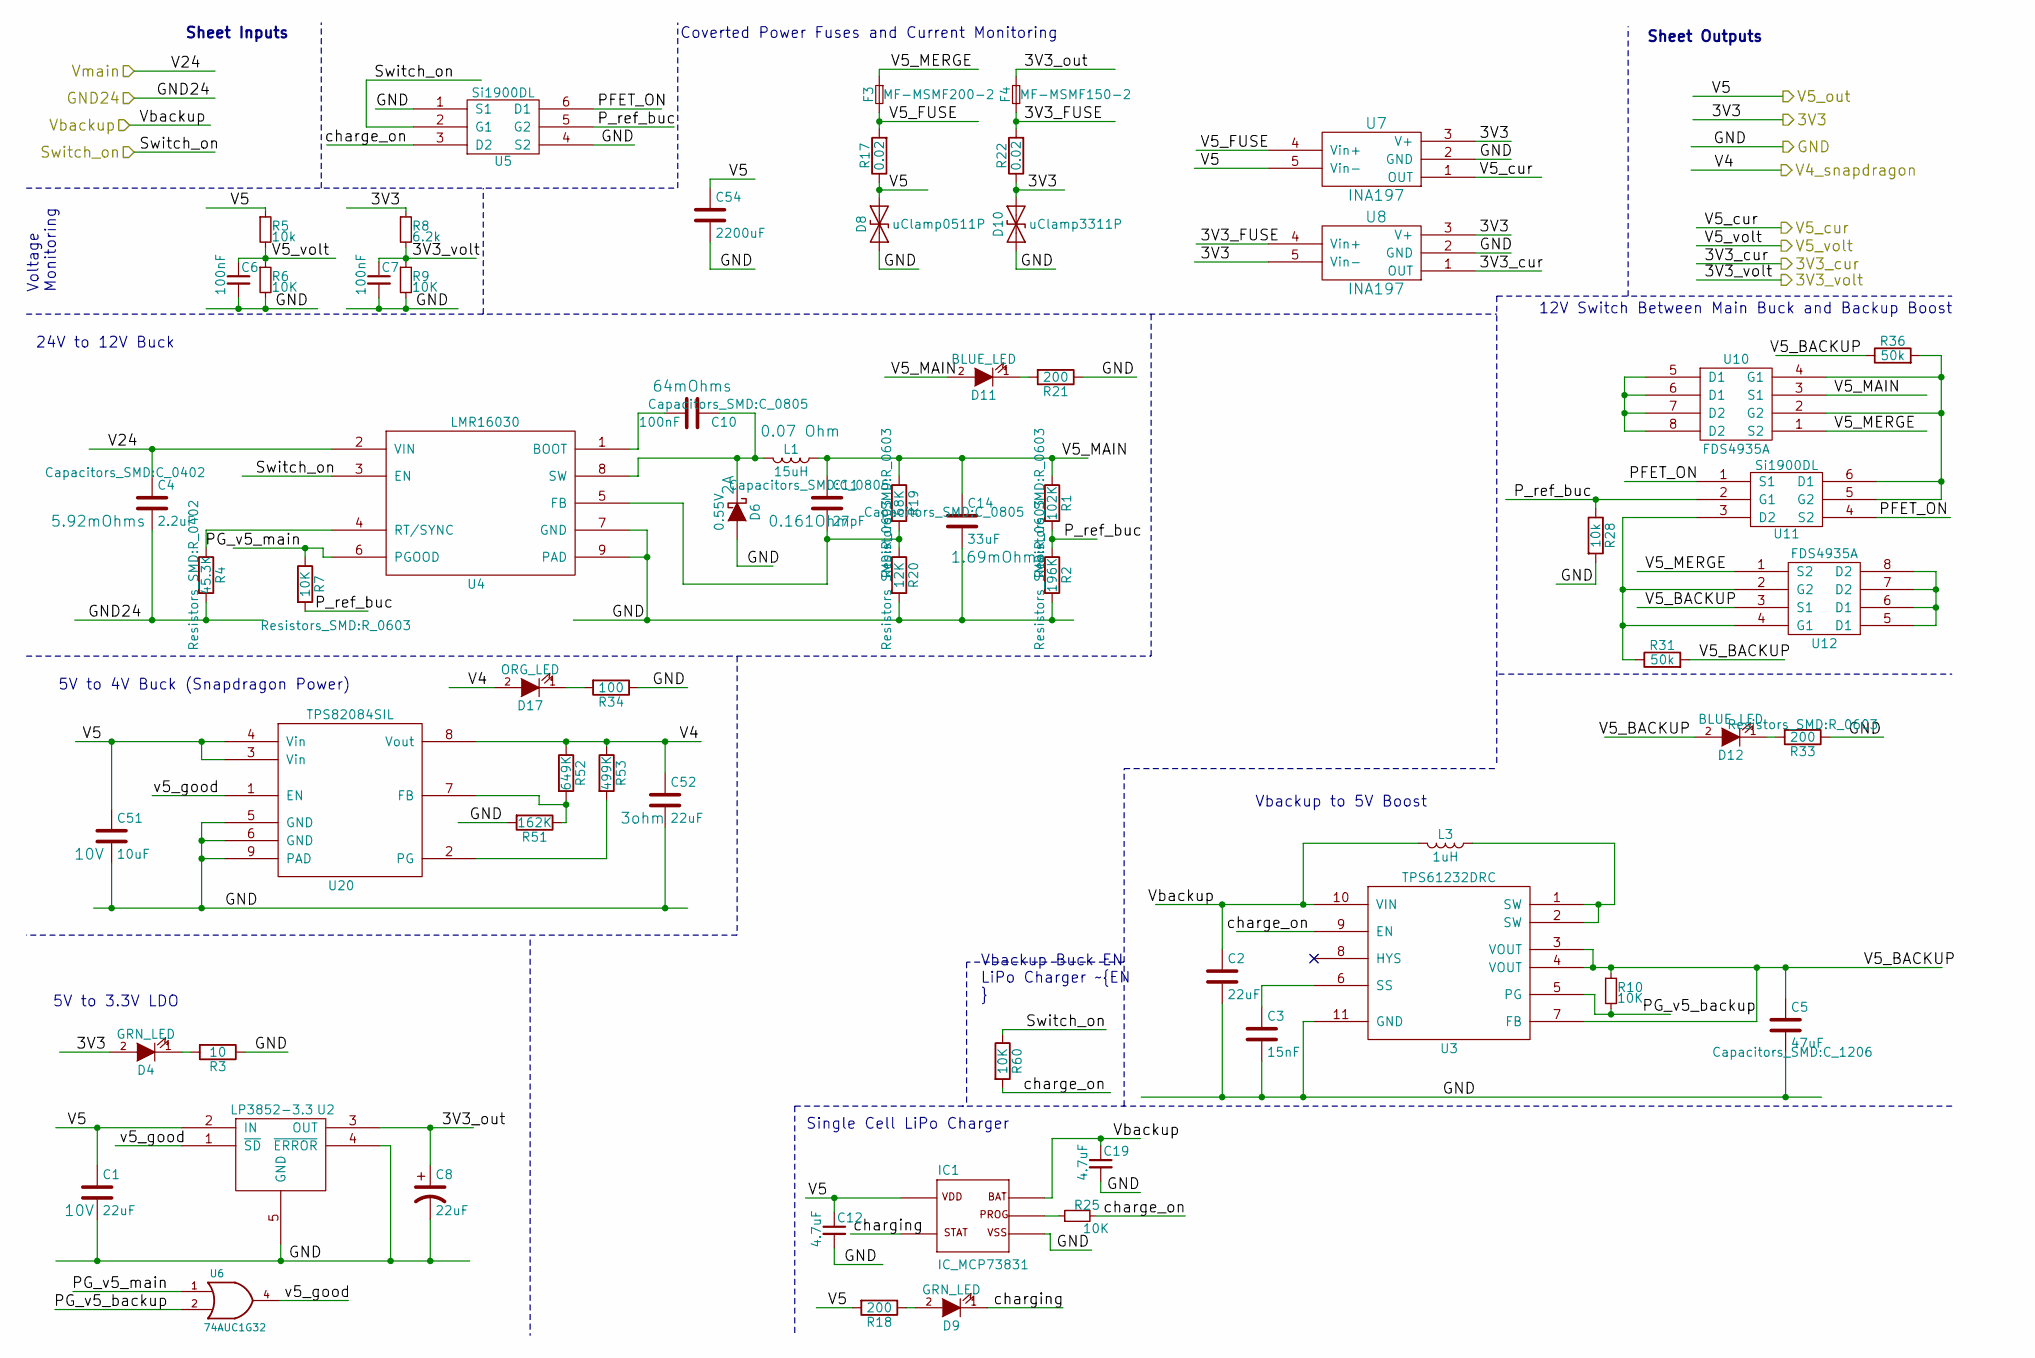
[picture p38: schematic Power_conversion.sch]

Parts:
C1: 22uF; C_0603; Voltage 10V
C2: 22uF; C_0805; Voltage 6.3V
C3: 15nF; C_0402; Voltage 16V
C4: 2.2uF; C_0402
C5: 47uF; C_1206
C6, C7: 100nF; C_0603
C8: 22uF; C_0603
C10: 100nF; C_0805
C11: 27pF; C_0805
C12, C19: 4.7uF; C_0603
C14: 33uF; C_0805
C51: 10uF; C_0805; Voltage 10V
C52: 22uF; C_1210
C54: 2200uF; CP_Tantalum_Case-U_EIA-6032-15_Reflow
D4, D9: GRN_LED; LED_0603
D6: 0.55V; SOD-123
D8: uClamp0511P; SLP1006P2
D10: uClamp3311P; SLP1006P2
D11, D12: BLUE_LED; LED_0603
D17: ORG_LED; LED_0603
F3: MF-MSMF200-2; SMD-1812
F4: MF-MSMF150-2; SMD-1812
IC1: IC_MCP73831; dp_devices-SOT-23-5
L1: 15uH; Bourns-8040
L3: 1uH; IHLP-2020BZ
R1: 102K; R_0603
R2: 196K; R_0603
R3: 10; R_0603
R4: 45.3K; R_0402
R5, R28: 10k; R_0603
R6, R7, R9, R10, R25, R60: 10K; R_0603
R8: 6.2k; R_0603
R17, R22: 0.02; R_0603
R18, R21, R33: 200; R_0603
R19: 68K; R_0603
R20: 12K; R_0603
R31, R36: 50k; R_0603
R34: 100; R_0603
R51: 162K; R_0402
R52: 649K; R_0402
R53: 499K; R_0402
U2: LP3852-3.3; SOT-223
U3: TPS61232DRC; DFN-10-1EP_3x3mm_Pitch0.5mm
U4: LMR16030; HSOIC-8-1EP_Pitch1.27mm
U5, U11: Si1900DL; SOT323-6
U6: 74AUC1G32; SO-70
U7, U8: INA197; dp_devices-SOT-23-5
U10, U12: FDS4935A; dp_devices-SO-8
U20: TPS82084SIL; uSIP-8

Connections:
+3V3: D4.2 (A), D10.2 (A2), R8.1, R22.1, U6.5 (VCC), U7.3 (V+), U8.3 (V+), U8.5 (Vin-); also elsewhere on the board
+5V: C1.1, C12.1, C51.1, C54.1, D8.2 (A2), IC1.4 (VDD), R5.1, R17.1, R18.2, U2.2 (IN), U7.5 (Vin-), U20.3 (Vin), U20.4 (Vin); also elsewhere on the board
+24V: C4.1, U4.2 (VIN); also elsewhere on the board
/3V3_cur: U8.1 (OUT); also elsewhere on the board
/3V3_volt: C7.1, R8.2, R9.1; also elsewhere on the board
/Power_conversion/3V3_FUSE: F4.2, R22.2, U8.4 (Vin+)
/Power_conversion/3V3_out: C8.1, F4.1, U2.3 (OUT)
/Power_conversion/PFET_ON: U5.6 (D1), U11.1 (S1), U11.4 (S2)
/Power_conversion/PG_v5_backup: R10.2, U3.5 (PG), U6.2
/Power_conversion/PG_v5_main: R7.1, U4.6 (PGOOD), U6.1
/Power_conversion/P_ref_buc: R1.2, R2.1, R7.2, R28.1, U5.5 (G2), U11.2 (G1)
/Power_conversion/V5_BACKUP: C5.1, D12.2 (A), R10.1, R31.2, R36.1, U3.3 (VOUT), U3.4 (VOUT), U3.7 (FB), U12.3 (S1)
/Power_conversion/V5_FUSE: F3.2, R17.2, U7.4 (Vin+)
/Power_conversion/V5_MAIN: C11.1, C14.1, D11.2 (A), L1.1, R1.1, R19.1, U10.3 (S1)
/Power_conversion/V5_MERGE: F3.1, U10.1 (S2), U12.1 (S2)
/Power_conversion/charge_on: R25.2, R60.2, U3.9 (EN), U5.3 (D2)
/Power_conversion/charging: D9.1 (K), IC1.1 (STAT)
/Power_conversion/v5_good: U2.1 (~SD), U6.4, U20.1 (EN)
/Switch_on: R60.1, U4.3 (EN), U5.2 (G1); also elsewhere on the board
/V4: C52.1, D17.2 (A), R52.1, R53.1, U20.8 (Vout); also elsewhere on the board
/V5_cur: U7.1 (OUT); also elsewhere on the board
/V5_volt: C6.1, R5.2, R6.1; also elsewhere on the board
/Vbackup_in: C2.1, C19.1, IC1.3 (BAT), L3.2, U3.10 (VIN); also elsewhere on the board
GND: C1.2, C2.2, C3.2, C5.2, C6.2, C7.2, C8.2, C12.2, C14.2, C19.2, C51.2, C52.2, C54.2, D6.2 (A), D8.1 (A1), D10.1 (A1), IC1.2 (VSS), R2.2, R3.1, R6.2, R9.2, R20.2, R21.1, R28.2, R33.1, R34.1, R51.2, U2.4 (~ERROR), U2.5 (GND), U3.11 (GND), U4.7 (GND), U4.9 (PAD), U5.1 (S1), U5.4 (S2), U6.3 (GND), U7.2 (GND), U8.2 (GND), U20.5 (GND), U20.6 (GND), U20.9 (PAD); also elsewhere on the board
GNDPWR: C4.2, R4.2; also elsewhere on the board
unnamed: C3.1, U3.6 (SS)
unnamed: C10.1, D6.1 (K), L1.2, U4.8 (SW)
unnamed: C10.2, U4.1 (BOOT)
unnamed: C11.2, R19.2, R20.1, U4.5 (FB)
unnamed: D4.1 (K), R3.2
unnamed: D9.2 (A), R18.1
unnamed: D11.1 (K), R21.2
unnamed: D12.1 (K), R33.2
unnamed: D17.1 (K), R34.2
unnamed: IC1.5 (PROG), R25.1
unnamed: L3.1, U3.1 (SW), U3.2 (SW)
unnamed: R4.1, U4.4 (RT/SYNC)
unnamed: R31.1, U11.3 (D2), U12.2 (G2), U12.4 (G1)
unnamed: R36.2, U10.2 (G2), U10.4 (G1), U11.5 (G2), U11.6 (D1)
unnamed: R51.1, R52.2, U20.7 (FB)
unnamed: R53.2, U20.2 (PG)
unnamed: U10.5 (D1), U10.6 (D1), U10.7 (D2), U10.8 (D2)
unnamed: U12.5 (D1), U12.6 (D1), U12.7 (D2), U12.8 (D2)

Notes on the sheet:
Sheet Outputs
Sheet Inputs
24V to 12V Buck
5V to 3.3V LDO
12V Switch Between Main Buck and Backup Boost
Coverted Power Fuses and Current Monitoring
Voltage Monitoring
Single Cell LiPo Charger
5V to 4V Buck (Snapdragon Power)
Vbackup to 5V Boost
Vbackup Buck EN LiPo Charger ~EN

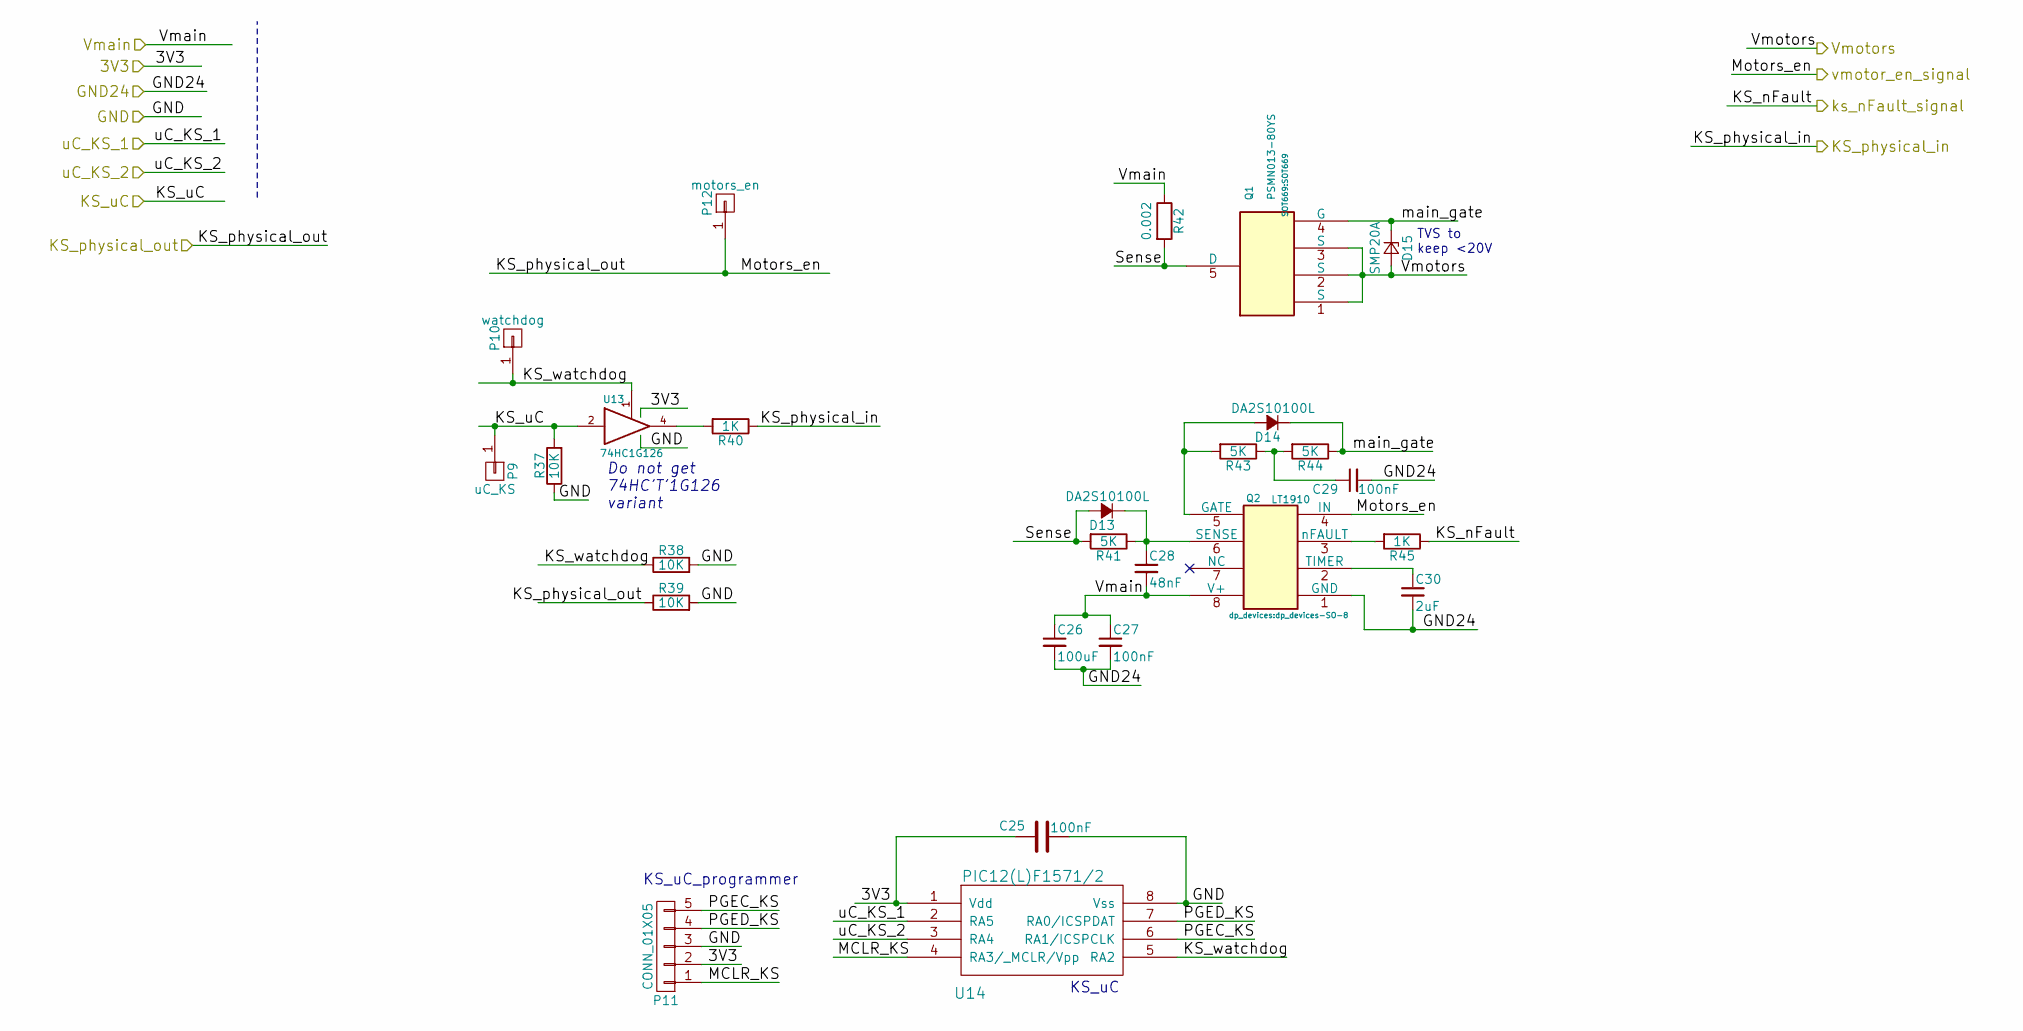
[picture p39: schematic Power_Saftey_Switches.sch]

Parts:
C25, C27, C29: 100nF; C_0603
C26: 100uF; C_1206
C28: 48nF; C_0603
C30: 2uF; C_0603
D13, D14: DA2S10100L; SSMini2-F5-B
D15: SMP20A; DO-220AA
P9: uC_KS; Pin_Header_Straight_1x01_Pitch2.00mm
P10: watchdog; Pin_Header_Straight_1x01_Pitch2.00mm
P11: CONN_01X05; Pin_Header_Angled_1x05_Pitch1.27mm
P12: motors_en; Pin_Header_Straight_1x01_Pitch2.00mm
Q1: PSMN013-80YS; SOT669
Q2: LT1910; dp_devices-SO-8
R37, R38, R39: 10K; R_0603
R40, R45: 1K; R_0603
R41, R43, R44: 5K; R_0603
R42: 0.002; R_1210
U13: 74HC1G126; SOT-353
U14: PIC12(L)F1571/2; dp_devices-SOIC-8

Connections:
+3V3: C25.1, P11.2, U13.5 (VCC), U14.1 (Vdd); also elsewhere on the board
+24V: C26.1, C27.1, C28.2, Q2.8 (V+), R42.1; also elsewhere on the board
/KS_physical_in: R40.1; also elsewhere on the board
/KS_physical_out: P12.1, Q2.4 (IN), R39.1; also elsewhere on the board
/KS_uC: P9.1, R37.2, U13.2; also elsewhere on the board
/Power_Saftey_Switches/KS_watchdog: P10.1, R38.1, U13.1, U14.5 (RA2)
/Power_Saftey_Switches/MCLR_KS: P11.1, U14.4 (RA3/_MCLR/Vpp)
/Power_Saftey_Switches/PGEC_KS: P11.5, U14.6 (RA1/ICSPCLK)
/Power_Saftey_Switches/PGED_KS: P11.4, U14.7 (RA0/ICSPDAT)
/Power_Saftey_Switches/Sense: D13.2 (A), Q1.5 (D), R41.2, R42.2
/Power_Saftey_Switches/main_gate: D14.1 (K), D15.1 (K), Q1.4 (G), R44.1
/Vmotors: D15.2 (A), Q1.1 (S), Q1.2 (S), Q1.3 (S); also elsewhere on the board
/ks_nFault_signal: R45.1; also elsewhere on the board
/uC_KS_1: U14.2 (RA5); also elsewhere on the board
/uC_KS_2: U14.3 (RA4); also elsewhere on the board
GND: C25.2, P11.3, R37.1, R38.2, R39.2, U13.3 (GND), U14.8 (Vss); also elsewhere on the board
GNDPWR: C26.2, C27.2, C29.2, C30.2, Q2.1 (GND); also elsewhere on the board
unnamed: C28.1, D13.1 (K), Q2.6 (SENSE), R41.1
unnamed: C29.1, R43.1, R44.2
unnamed: C30.1, Q2.2 (TIMER)
unnamed: D14.2 (A), Q2.5 (GATE), R43.2
unnamed: Q2.3 (nFAULT), R45.2
unnamed: R40.2, U13.4

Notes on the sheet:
TVS to keep <20V
Do not get 74HC'T'1G126 variant
KS_uC_programmer
KS_uC

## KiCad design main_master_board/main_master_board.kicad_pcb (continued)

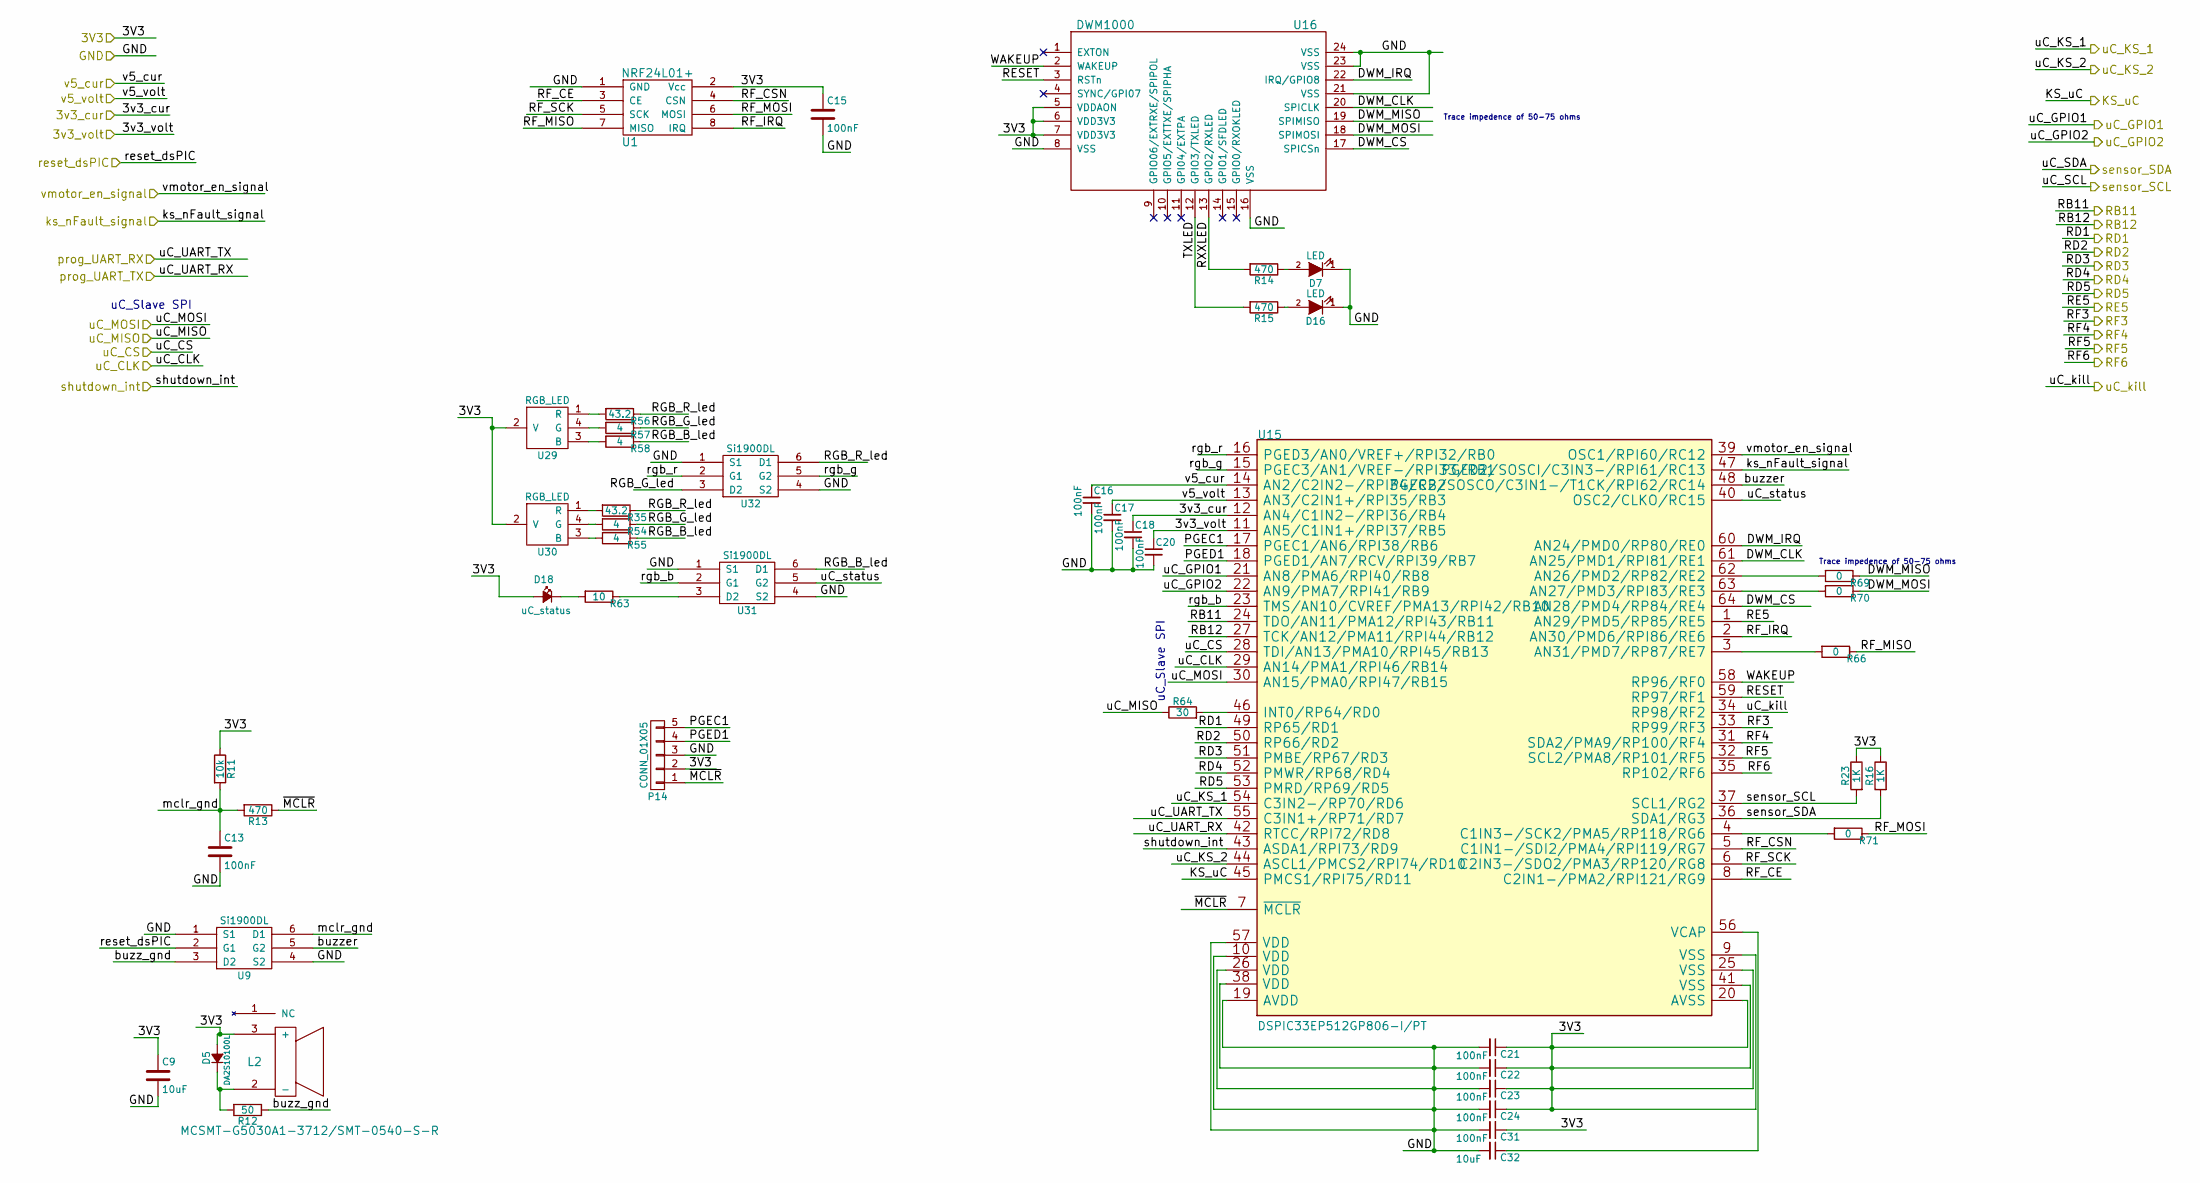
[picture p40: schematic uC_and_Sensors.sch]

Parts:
C9, C32: 10uF; C_0603
C13, C15: 100nF; C_0603
C16, C17, C18, C20, C21, C22, C23, C24, C31: 100nF; C_0402
D5: DA2S10100L; SSMini2-F5-B
D7, D16: LED; LED_0603
D18: uC_status; LED_0603
L2: MCSMT-G5030A1-3712/SMT-0540-S-R; MCSMT-G5030A1-3712
P14: CONN_01X05; Pin_Header_Angled_1x05_Pitch1.27mm
R11: 10k; R_0603
R12: 50; R_0603
R13, R14, R15: 470; R_0603
R16, R23: 1K; R_0603
R35, R56: 43.2; R_0402
R54, R55, R57, R58: 4; R_0402
R63: 10; R_0402
R64: 30; R_0402
R66, R69, R70, R71: 0; R_0603
U1: NRF24L01+; nRF24L01_Breakout
U9, U31, U32: Si1900DL; SOT323-6
U15: DSPIC33EP512GP806-I/PT; dp_devices-TQFP-64-10X10
U16: DWM1000; dmw1000
U29, U30: RGB_LED; APFA2507QBDSEEZGKC

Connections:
+3V3: C9.1, C15.1, C21.1, C22.1, C23.1, C24.1, C31.1, D5.2 (A), D18.2 (A), L2.3 (+), P14.2, R11.1, R16.1, R23.1, U1.2 (Vcc), U15.9 (VSS), U15.20 (AVSS), U15.25 (VSS), U15.41 (VSS), U16.5 (VDDAON), U16.6 (VDD3V3), U16.7 (VDD3V3), U29.2 (V), U30.2 (V); also elsewhere on the board
/3V3_cur: C18.1, U15.12 (AN4/C1IN2-/RPI36/RB4); also elsewhere on the board
/3V3_volt: C20.1, U15.11 (AN5/C1IN1+/RPI37/RB5); also elsewhere on the board
/KS_physical_out: U15.39 (OSC1/RPI60/RC12); also elsewhere on the board
/KS_uC: U15.45 (PMCS1/RPI75/RD11); also elsewhere on the board
/RB11: U15.24 (TDO/AN11/PMA12/RPI43/RB11); also elsewhere on the board
/RB12: U15.27 (TCK/AN12/PMA11/RPI44/RB12); also elsewhere on the board
/RD1: U15.49 (RP65/RD1); also elsewhere on the board
/RD2: U15.50 (RP66/RD2); also elsewhere on the board
/RD3: U15.51 (PMBE/RP67/RD3); also elsewhere on the board
/RD4: U15.52 (PMWR/RP68/RD4); also elsewhere on the board
/RD5: U15.53 (PMRD/RP69/RD5); also elsewhere on the board
/RE5: U15.1 (AN29/PMD5/RP85/RE5); also elsewhere on the board
/RF3: U15.33 (RP99/RF3); also elsewhere on the board
/RF4: U15.31 (SDA2/PMA9/RP100/RF4); also elsewhere on the board
/RF5: U15.32 (SCL2/PMA8/RP101/RF5); also elsewhere on the board
/RF6: U15.35 (RP102/RF6); also elsewhere on the board
/V5_cur: C16.1, U15.14 (AN2/C2IN2-/RPI34/RB2); also elsewhere on the board
/V5_volt: C17.1, U15.13 (AN3/C2IN1+/RPI35/RB3); also elsewhere on the board
/ks_nFault_signal: U15.47 (PGED2/SOSCI/C3IN3-/RPI61/RC13); also elsewhere on the board
/prog_rx: U15.42 (RTCC/RPI72/RD8); also elsewhere on the board
/prog_tx: U15.55 (C3IN1+/RP71/RD7); also elsewhere on the board
/reset_dsPIC: U9.2 (G1); also elsewhere on the board
/sensor_SCL: R23.2, U15.37 (SCL1/RG2); also elsewhere on the board
/sensor_SDA: R16.2, U15.36 (SDA1/RG3); also elsewhere on the board
/shutdown_int: U15.43 (ASDA1/RPI73/RD9); also elsewhere on the board
/uC_CLK: U15.29 (AN14/PMA1/RPI46/RB14); also elsewhere on the board
/uC_CS: U15.28 (TDI/AN13/PMA10/RPI45/RB13); also elsewhere on the board
/uC_GPIO1: U15.21 (AN8/PMA6/RPI40/RB8); also elsewhere on the board
/uC_GPIO2: U15.22 (AN9/PMA7/RPI41/RB9); also elsewhere on the board
/uC_KS_1: U15.54 (C3IN2-/RP70/RD6); also elsewhere on the board
/uC_KS_2: U15.44 (ASCL1/PMCS2/RPI74/RD10); also elsewhere on the board
/uC_MISO: R64.1; also elsewhere on the board
/uC_MOSI: U15.30 (AN15/PMA0/RPI47/RB15); also elsewhere on the board
/uC_and_Sensors/DWM_CLK: U15.61 (AN25/PMD1/RPI81/RE1), U16.20 (SPICLK)
/uC_and_Sensors/DWM_CS: U15.64 (AN28/PMD4/RP84/RE4), U16.17 (SPICSn)
/uC_and_Sensors/DWM_IRQ: U15.60 (AN24/PMD0/RP80/RE0), U16.22 (IRQ/GPIO8)
/uC_and_Sensors/DWM_MISO: R69.1, U16.19 (SPIMISO)
/uC_and_Sensors/DWM_MOSI: R70.1, U16.18 (SPIMOSI)
/uC_and_Sensors/PGEC1: P14.5, U15.17 (PGEC1/AN6/RPI38/RB6)
/uC_and_Sensors/PGED1: P14.4, U15.18 (PGED1/AN7/RCV/RPI39/RB7)
/uC_and_Sensors/RESET: U15.59 (RP97/RF1), U16.3 (RSTn)
/uC_and_Sensors/RF_CE: U1.3 (CE), U15.8 (C2IN1-/PMA2/RPI121/RG9)
/uC_and_Sensors/RF_CSN: U1.4 (CSN), U15.5 (C1IN1-/SDI2/PMA4/RPI119/RG7)
/uC_and_Sensors/RF_IRQ: U1.8 (IRQ), U15.2 (AN30/PMD6/RPI86/RE6)
/uC_and_Sensors/RF_MISO: R66.1, U1.7 (MISO)
/uC_and_Sensors/RF_MOSI: R71.1, U1.6 (MOSI)
/uC_and_Sensors/RF_SCK: U1.5 (SCK), U15.6 (C2IN3-/SDO2/PMA3/RP120/RG8)
/uC_and_Sensors/RGB_B_led: R55.1, R58.1, U31.6 (D1)
/uC_and_Sensors/RGB_G_led: R54.1, R57.1, U32.3 (D2)
/uC_and_Sensors/RGB_R_led: R35.1, R56.1, U32.6 (D1)
/uC_and_Sensors/RXXLED: R14.2, U16.13 (GPIO2/RXLED)
/uC_and_Sensors/TXLED: R15.2, U16.12 (GPIO3/TXLED)
/uC_and_Sensors/WAKEUP: U15.58 (RP96/RF0), U16.2 (WAKEUP)
/uC_and_Sensors/buzz_gnd: R12.1, U9.3 (D2)
/uC_and_Sensors/buzzer: U9.5 (G2), U15.48 (PGEC2/SOSCO/C3IN1-/T1CK/RPI62/RC14)
/uC_and_Sensors/mclr_gnd: C13.1, R11.2, R13.2, U9.6 (D1)
/uC_and_Sensors/rgb_b: U15.23 (TMS/AN10/CVREF/PMA13/RPI42/RB10), U31.2 (G1)
/uC_and_Sensors/rgb_g: U15.15 (PGEC3/AN1/VREF-/RPI33/RB1), U32.5 (G2)
/uC_and_Sensors/rgb_r: U15.16 (PGED3/AN0/VREF+/RPI32/RB0), U32.2 (G1)
/uC_and_Sensors/uC_status: U15.40 (OSC2/CLKO/RC15), U31.5 (G2)
/uC_and_Sensors/~MCLR: P14.1, R13.1, U15.7 (~MCLR)
/uC_pwr_kill: U15.34 (RP98/RF2); also elsewhere on the board
GND: C9.2, C13.2, C15.2, C16.2, C17.2, C18.2, C20.2, C21.2, C22.2, C23.2, C24.2, C31.2, C32.2, D7.1 (K), D16.1 (K), P14.3, U1.1 (GND), U9.1 (S1), U9.4 (S2), U15.10 (VDD), U15.19 (AVDD), U15.26 (VDD), U15.38 (VDD), U15.57 (VDD), U16.8 (VSS), U16.16 (VSS), U16.21 (VSS), U16.23 (VSS), U16.24 (VSS), U31.1 (S1), U31.4 (S2), U32.1 (S1), U32.4 (S2); also elsewhere on the board
unnamed: C32.1, U15.56 (VCAP)
unnamed: D5.1 (K), L2.2 (-), R12.2
unnamed: D7.2 (A), R14.1
unnamed: D16.2 (A), R15.1
unnamed: D18.1 (K), R63.2
unnamed: R35.2, U30.1 (R)
unnamed: R54.2, U30.4 (G)
unnamed: R55.2, U30.3 (B)
unnamed: R56.2, U29.1 (R)
unnamed: R57.2, U29.4 (G)
unnamed: R58.2, U29.3 (B)
unnamed: R63.1, U31.3 (D2)
unnamed: R64.2, U15.46 (INT0/RP64/RD0)
unnamed: R66.2, U15.3 (AN31/PMD7/RP87/RE7)
unnamed: R69.2, U15.62 (AN26/PMD2/RP82/RE2)
unnamed: R70.2, U15.63 (AN27/PMD3/RPI83/RE3)
unnamed: R71.2, U15.4 (C1IN3-/SCK2/PMA5/RP118/RG6)

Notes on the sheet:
uC_Slave SPI
Trace impedence of 50-75 ohms

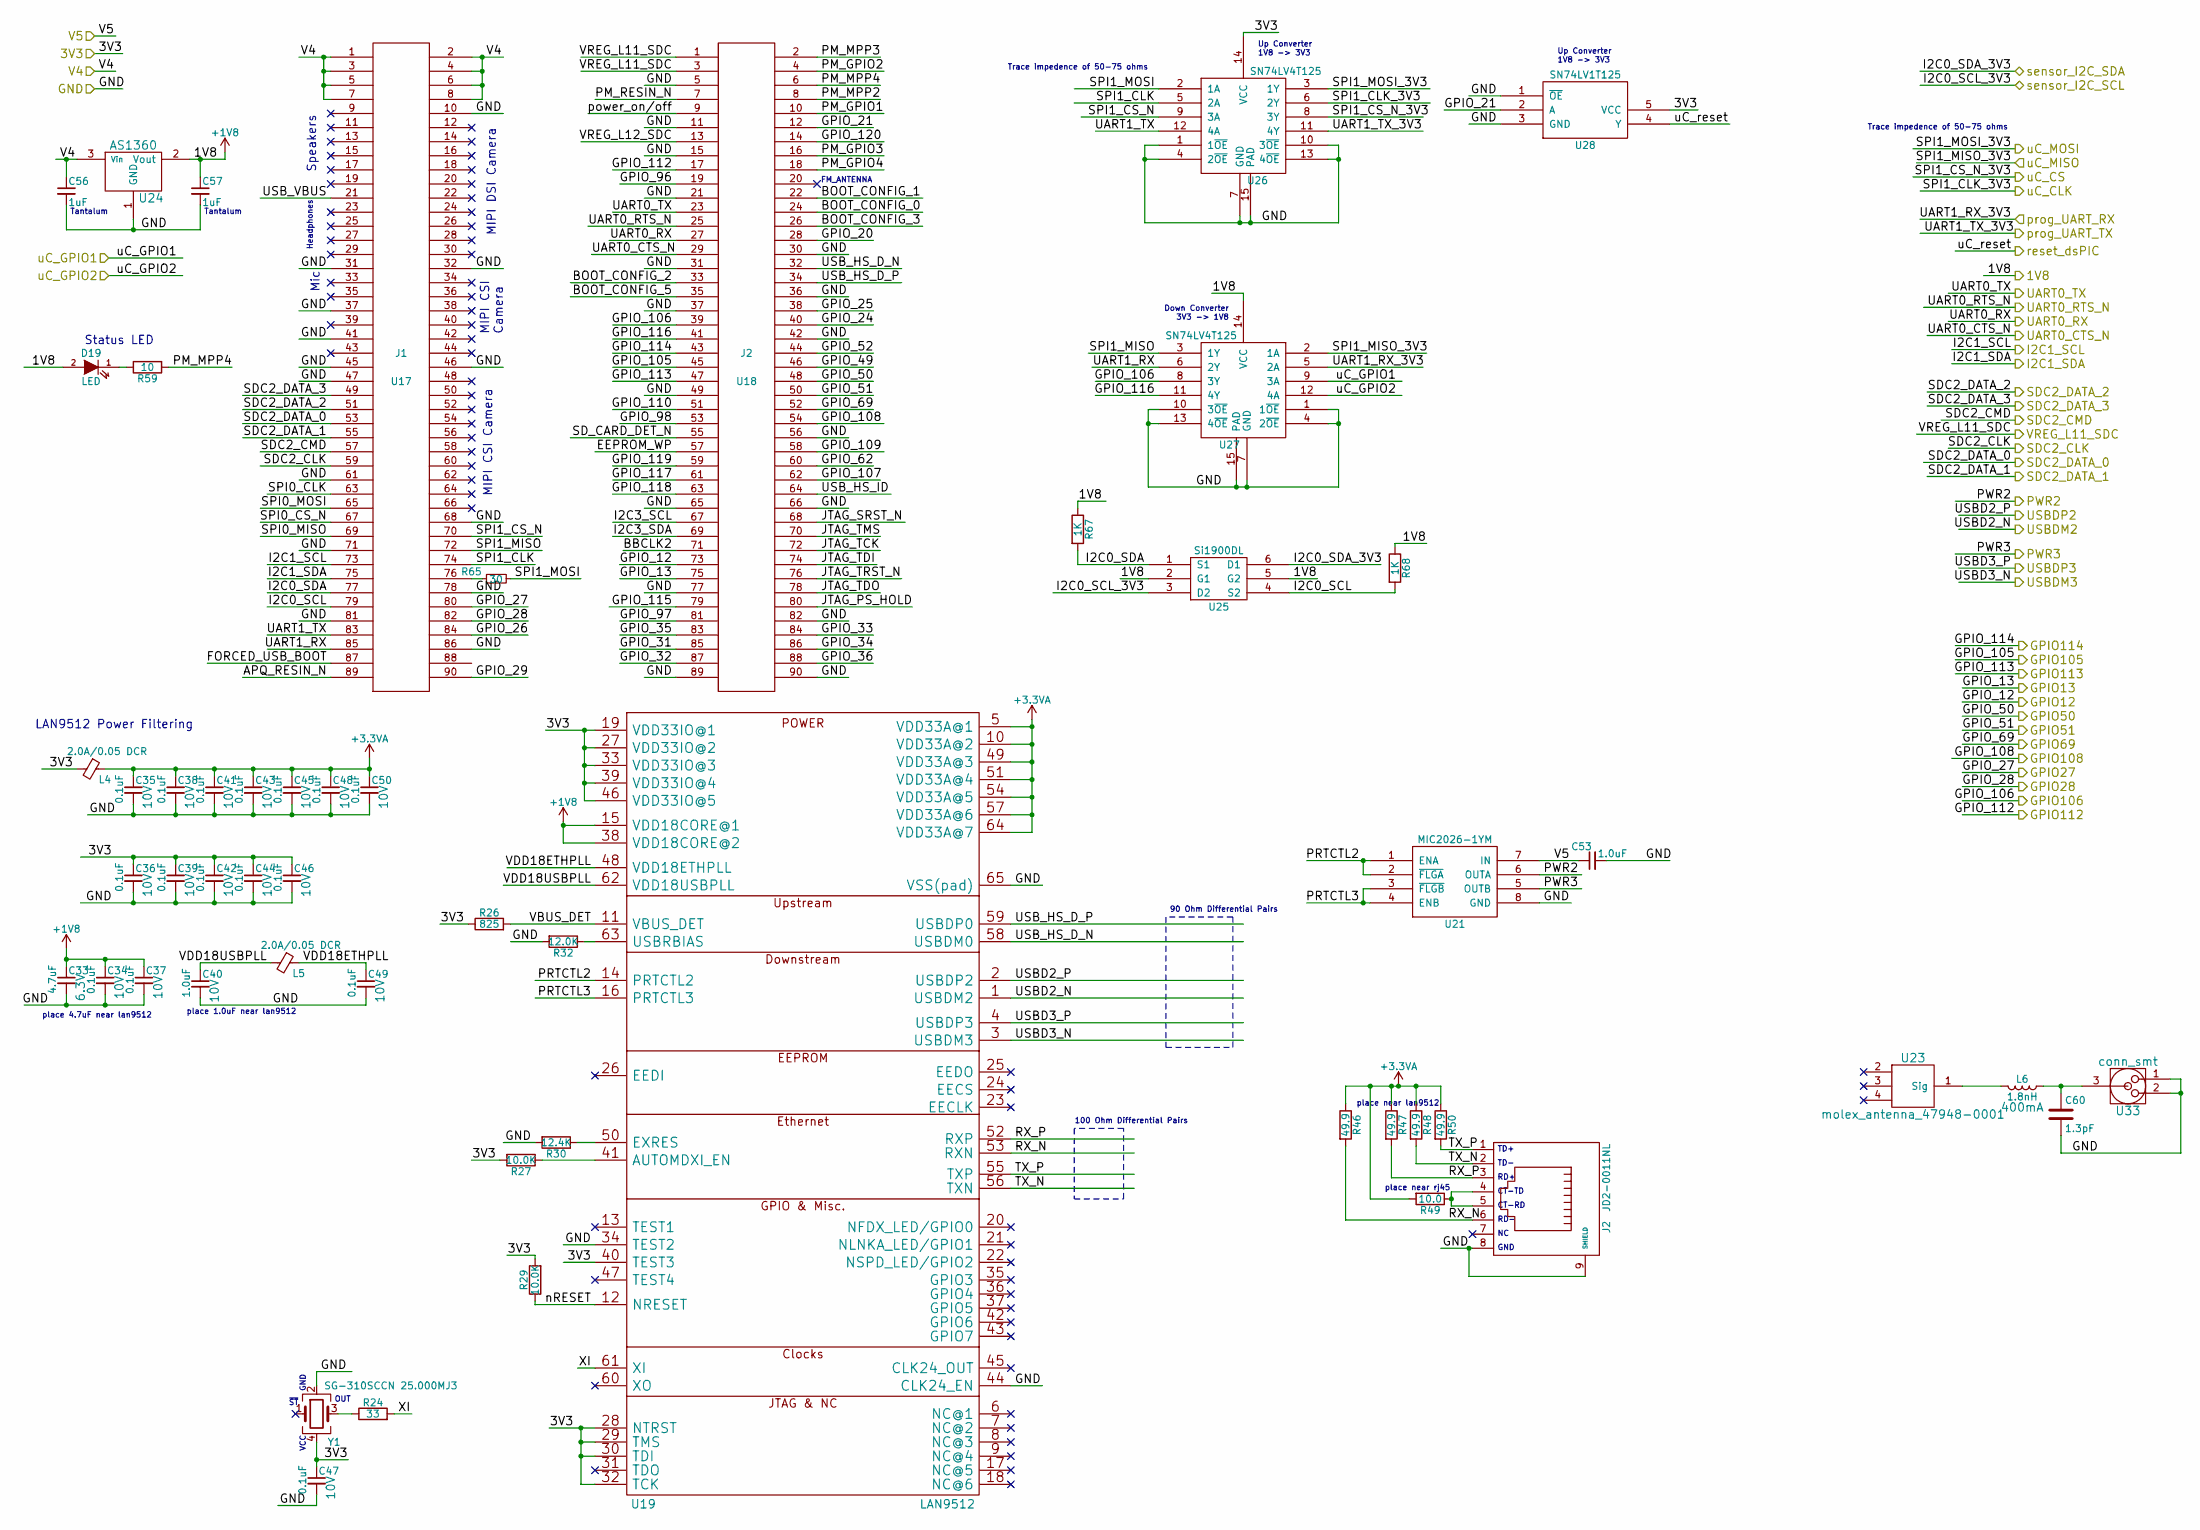
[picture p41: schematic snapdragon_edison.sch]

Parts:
C33: 4.7uF; C_0603; Voltage 6.3V
C34, C35, C36, C37, C38, C39, C41, C42, C43, C44, C45, C46, C47, C48, C49, C50: 0.1uF; C_0402; Voltage 10V
C40: 1.0uF; C_0402; Voltage 10V
C53: 1.0uF; C_0603
C56, C57: 1uF; C_0603
C60: 1.3pF; C_0402
D19: LED; LED_0603
J2: JD2-0011NL
L4, L5: 2.0A/0.05 DCR; dp_devices-C603
L6: 1.8nH; R_0402
R24: 33; R_0402
R26: 825; R_0402
R27, R29: 10.0K; R_0402
R30: 12.4K; R_0402
R32: 12.0K; R_0402
R46, R47, R48, R50: 49.9; R_0402
R49: 10.0; R_0402
R59: 10; R_0603
R65: 30; R_0402
R67, R68: 1K; R_0402
U17: J1; DART-SD410
U18: J2; DF40HC(3.0)-90DS-0.4V(51)
U19: LAN9512; QFN-64-1EP_9x9mm_Pitch0.5mm
U21: MIC2026-1YM; SOIC-8_N
U23: molex_antenna_47948-0001; Molex_47948-0001
U24: AS1360; SOT-23
U25: Si1900DL; SOT323-6
U26, U27: SN74LV4T125; VQFN-14
U28: SN74LV1T125; SO-70
U33: conn_smt; U.FL-R-SMT-1(01)
Y1: SG-310SCCN 25.000MJ3; SG-310

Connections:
+1V8: C33.1, C34.1, C37.1, C57.1, D19.2 (A), R67.1, R68.1, U19.15 (VDD18CORE@1), U19.38 (VDD18CORE@2), U24.2 (Vout), U25.2 (G1), U25.5 (G2), U27.14 (VCC); also elsewhere on the board
+3.3VA: C35.1, C38.1, C41.1, C43.1, C45.1, C48.1, C50.1, L4.1, R46.1, R47.1, R48.1, R49.2, R50.1, U19.5 (VDD33A@1), U19.10 (VDD33A@2), U19.49 (VDD33A@3), U19.51 (VDD33A@4), U19.54 (VDD33A@5), U19.57 (VDD33A@6), U19.64 (VDD33A@7)
+3V3: C36.1, C39.1, C42.1, C44.1, C46.1, C47.1, L4.2, R26.1, R27.2, R29.2, U19.19 (VDD33IO@1), U19.27 (VDD33IO@2), U19.28 (NTRST), U19.29 (TMS), U19.30 (TDI), U19.32 (TCK), U19.33 (VDD33IO@3), U19.39 (VDD33IO@4), U19.40 (TEST3), U19.46 (VDD33IO@5), U26.14 (VCC), U28.5 (VCC), Y1.4; also elsewhere on the board
+5V: C53.1, U21.7 (IN); also elsewhere on the board
/GPIO_12: U18.73; also elsewhere on the board
/GPIO_13: U18.75; also elsewhere on the board
/GPIO_27: U17.80; also elsewhere on the board
/GPIO_28: U17.82; also elsewhere on the board
/GPIO_50: U18.48; also elsewhere on the board
/GPIO_51: U18.50; also elsewhere on the board
/GPIO_69: U18.52; also elsewhere on the board
/GPIO_105: U18.43; also elsewhere on the board
/GPIO_106: U18.39, U27.8 (3Y)
/GPIO_108: U18.54; also elsewhere on the board
/GPIO_112: U18.17; also elsewhere on the board
/GPIO_113: U18.47
/GPIO_114: U18.45; also elsewhere on the board
/I2C1_SCL: U17.73
/I2C1_SDA: U17.75
/PWR2: U21.6 (OUTA); also elsewhere on the board
/PWR3: U21.5 (OUTB); also elsewhere on the board
/SDC2_CLK: U17.59; also elsewhere on the board
/SDC2_CMD: U17.57; also elsewhere on the board
/SDC2_DATA_0: U17.53; also elsewhere on the board
/SDC2_DATA_1: U17.55; also elsewhere on the board
/SDC2_DATA_2: U17.51; also elsewhere on the board
/SDC2_DATA_3: U17.49; also elsewhere on the board
/UART0_CTS_N: U18.29; also elsewhere on the board
/UART0_RTS_N: U18.25; also elsewhere on the board
/UART0_RX: U18.27; also elsewhere on the board
/UART0_TX: U18.23; also elsewhere on the board
/USBD2_N: U19.1 (USBDM2); also elsewhere on the board
/USBD2_P: U19.2 (USBDP2); also elsewhere on the board
/USBD3_N: U19.3 (USBDM3); also elsewhere on the board
/USBD3_P: U19.4 (USBDP3); also elsewhere on the board
/V4: C56.1, U17.1, U17.2, U17.3, U17.4, U17.5, U17.6, U17.7, U17.8, U24.3 (Vin); also elsewhere on the board
/VREG_L11_SDC: U18.1, U18.3; also elsewhere on the board
/prog_rx: U27.5 (2A); also elsewhere on the board
/prog_tx: U26.11 (4Y); also elsewhere on the board
/reset_dsPIC: U28.4 (Y); also elsewhere on the board
/sensor_SCL: U25.3 (D2); also elsewhere on the board
/sensor_SDA: U25.6 (D1); also elsewhere on the board
/snapdragon_edison/APQ_RESIN_N: U17.89
/snapdragon_edison/BBCLK2: U18.71
/snapdragon_edison/BOOT_CONFIG_0: U18.24
/snapdragon_edison/BOOT_CONFIG_1: U18.22
/snapdragon_edison/BOOT_CONFIG_2: U18.33
/snapdragon_edison/BOOT_CONFIG_3: U18.26
/snapdragon_edison/BOOT_CONFIG_5: U18.35
/snapdragon_edison/EEPROM_WP: U18.57
/snapdragon_edison/FORCED_USB_BOOT: U17.87
/snapdragon_edison/GPIO_20: U18.28
/snapdragon_edison/GPIO_21: U18.12, U28.2 (A)
/snapdragon_edison/GPIO_24: U18.40
/snapdragon_edison/GPIO_25: U18.38
/snapdragon_edison/GPIO_26: U17.84
/snapdragon_edison/GPIO_29: U17.90
/snapdragon_edison/GPIO_31: U18.85
/snapdragon_edison/GPIO_32: U18.87
/snapdragon_edison/GPIO_33: U18.84
/snapdragon_edison/GPIO_34: U18.86
/snapdragon_edison/GPIO_35: U18.83
/snapdragon_edison/GPIO_36: U18.88
/snapdragon_edison/GPIO_49: U18.46
/snapdragon_edison/GPIO_52: U18.44
/snapdragon_edison/GPIO_62: U18.60
/snapdragon_edison/GPIO_96: U18.19
/snapdragon_edison/GPIO_97: U18.81
/snapdragon_edison/GPIO_98: U18.53
/snapdragon_edison/GPIO_107: U18.62
/snapdragon_edison/GPIO_109: U18.58
/snapdragon_edison/GPIO_110: U18.51
/snapdragon_edison/GPIO_115: U18.79
/snapdragon_edison/GPIO_116: U18.41, U27.11 (4Y)
/snapdragon_edison/GPIO_117: U18.61
/snapdragon_edison/GPIO_118: U18.63
/snapdragon_edison/GPIO_119: U18.59
/snapdragon_edison/GPIO_120: U18.14
/snapdragon_edison/I2C0_SCL: R68.2, U17.79, U25.4 (S2)
/snapdragon_edison/I2C0_SDA: R67.2, U17.77, U25.1 (S1)
/snapdragon_edison/I2C3_SCL: U18.67
/snapdragon_edison/I2C3_SDA: U18.69
/snapdragon_edison/JTAG_PS_HOLD: U18.80
/snapdragon_edison/JTAG_SRST_N: U18.68
/snapdragon_edison/JTAG_TCK: U18.72
/snapdragon_edison/JTAG_TDI: U18.74
/snapdragon_edison/JTAG_TDO: U18.78
/snapdragon_edison/JTAG_TMS: U18.70
/snapdragon_edison/JTAG_TRST_N: U18.76
/snapdragon_edison/PM_GPIO1: U18.10
/snapdragon_edison/PM_GPIO2: U18.4
/snapdragon_edison/PM_GPIO3: U18.16
/snapdragon_edison/PM_GPIO4: U18.18
/snapdragon_edison/PM_MPP2: U18.8
/snapdragon_edison/PM_MPP3: U18.2
/snapdragon_edison/PM_MPP4: R59.2, U18.6
/snapdragon_edison/PM_RESIN_N: U18.7
/snapdragon_edison/PRTCTL2: U19.14 (PRTCTL2), U21.1 (ENA), U21.2 (~FLGA)
/snapdragon_edison/PRTCTL3: U19.16 (PRTCTL3), U21.3 (~FLGB), U21.4 (ENB)
/snapdragon_edison/RX_N: J2.6, R46.2, U19.53 (RXN)
/snapdragon_edison/RX_P: J2.3, R47.2, U19.52 (RXP)
/snapdragon_edison/SD_CARD_DET_N: U18.55
/snapdragon_edison/SPI0_CLK: U17.63
/snapdragon_edison/SPI0_CS_N: U17.67
/snapdragon_edison/SPI0_MISO: U17.69
/snapdragon_edison/SPI0_MOSI: U17.65
/snapdragon_edison/SPI1_CLK: U17.74, U26.5 (2A)
/snapdragon_edison/SPI1_CS_N: U17.70, U26.9 (3A)
/snapdragon_edison/SPI1_MISO: U17.72, U27.3 (1Y)
/snapdragon_edison/SPI1_MOSI: R65.2, U26.2 (1A)
/snapdragon_edison/TX_N: J2.2, R48.2, U19.56 (TXN)
/snapdragon_edison/TX_P: J2.1, R50.2, U19.55 (TXP)
/snapdragon_edison/UART1_RX: U17.85, U27.6 (2Y)
/snapdragon_edison/UART1_TX: U17.83, U26.12 (4A)
/snapdragon_edison/USB_HS_D_N: U18.32, U19.58 (USBDM0)
/snapdragon_edison/USB_HS_D_P: U18.34, U19.59 (USBDP0)
/snapdragon_edison/USB_HS_ID: U18.64
/snapdragon_edison/USB_VBUS: U17.21
/snapdragon_edison/VBUS_DET: R26.2, U19.11 (VBUS_DET)
/snapdragon_edison/VDD18ETHPLL: C49.1, L5.1, U19.48 (VDD18ETHPLL)
/snapdragon_edison/VDD18USBPLL: C40.1, L5.2, U19.62 (VDD18USBPLL)
/snapdragon_edison/VREG_L12_SDC: U18.13
/snapdragon_edison/XI: R24.2, U19.61 (XI)
/snapdragon_edison/nRESET: R29.1, U19.12 (NRESET)
/snapdragon_edison/power_on/off: U18.9
/uC_CLK: U26.6 (2Y); also elsewhere on the board
/uC_CS: U26.8 (3Y); also elsewhere on the board
/uC_GPIO1: U27.9 (3A); also elsewhere on the board
/uC_GPIO2: U27.12 (4A); also elsewhere on the board
/uC_MISO: U27.2 (1A); also elsewhere on the board
/uC_MOSI: U26.3 (1Y); also elsewhere on the board
GND: C33.2, C34.2, C35.2, C36.2, C37.2, C38.2, C39.2, C40.2, C41.2, C42.2, C43.2, C44.2, C45.2, C46.2, C47.2, C48.2, C49.2, C50.2, C53.2, C56.2, C57.2, C60.2, J2.8, J2.9 (SHIELD), R30.2, R32.2, U17.10, U17.31, U17.32, U17.37, U17.41, U17.45, U17.46, U17.47, U17.61, U17.68, U17.71, U17.78, U17.81, U17.86, U18.5, U18.11, U18.15, U18.21, U18.30, U18.31, U18.36, U18.37, U18.42, U18.49, U18.56, U18.65, U18.66, U18.77, U18.82, U18.89, U18.90, U19.34 (TEST2), U19.44 (CLK24_EN), U19.65 (VSS(pad)), U21.8 (GND), U24.1 (GND), U26.1 (1~OE), U26.4 (2~OE), U26.7 (GND), U26.10 (3~OE), U26.13 (4~OE), U26.15 (PAD), U27.1 (1~OE), U27.4 (2~OE), U27.7 (GND), U27.10 (3~OE), U27.13 (4~OE), U27.15 (PAD), U28.1 (~OE), U28.3 (GND), U33.1, U33.2, Y1.2; also elsewhere on the board
unnamed: C60.1, L6.1, U33.3
unnamed: D19.1 (K), R59.1
unnamed: J2.4, J2.5, R49.1
unnamed: L6.2, U23.1 (Sig)
unnamed: R24.1, Y1.3
unnamed: R27.1, U19.41 (AUTOMDXI_EN)
unnamed: R30.1, U19.50 (EXRES)
unnamed: R32.1, U19.63 (USBRBIAS)
unnamed: R65.1, U17.76

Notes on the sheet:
MIPI CSI Camera
MIPI DSI Camera
Speakers
Headphones
Mic
MIPI CSI Camera
FM_ANTENNA
TD+
TD-
RD+
CT-TD
CT-RD
RD-
GND
LAN9512 Power Filtering
~ST
OUT
VCC
place near rj45
place near lan9512
100 Ohm Differential Pairs
90 Ohm Differential Pairs
place 1.0uF near lan9512
place 4.7uF near lan9512
Tantalum
Up Converter 1V8 -> 3V3
Down Converter 3V3 -> 1V8
Trace impedence of 50-75 ohms
Status LED

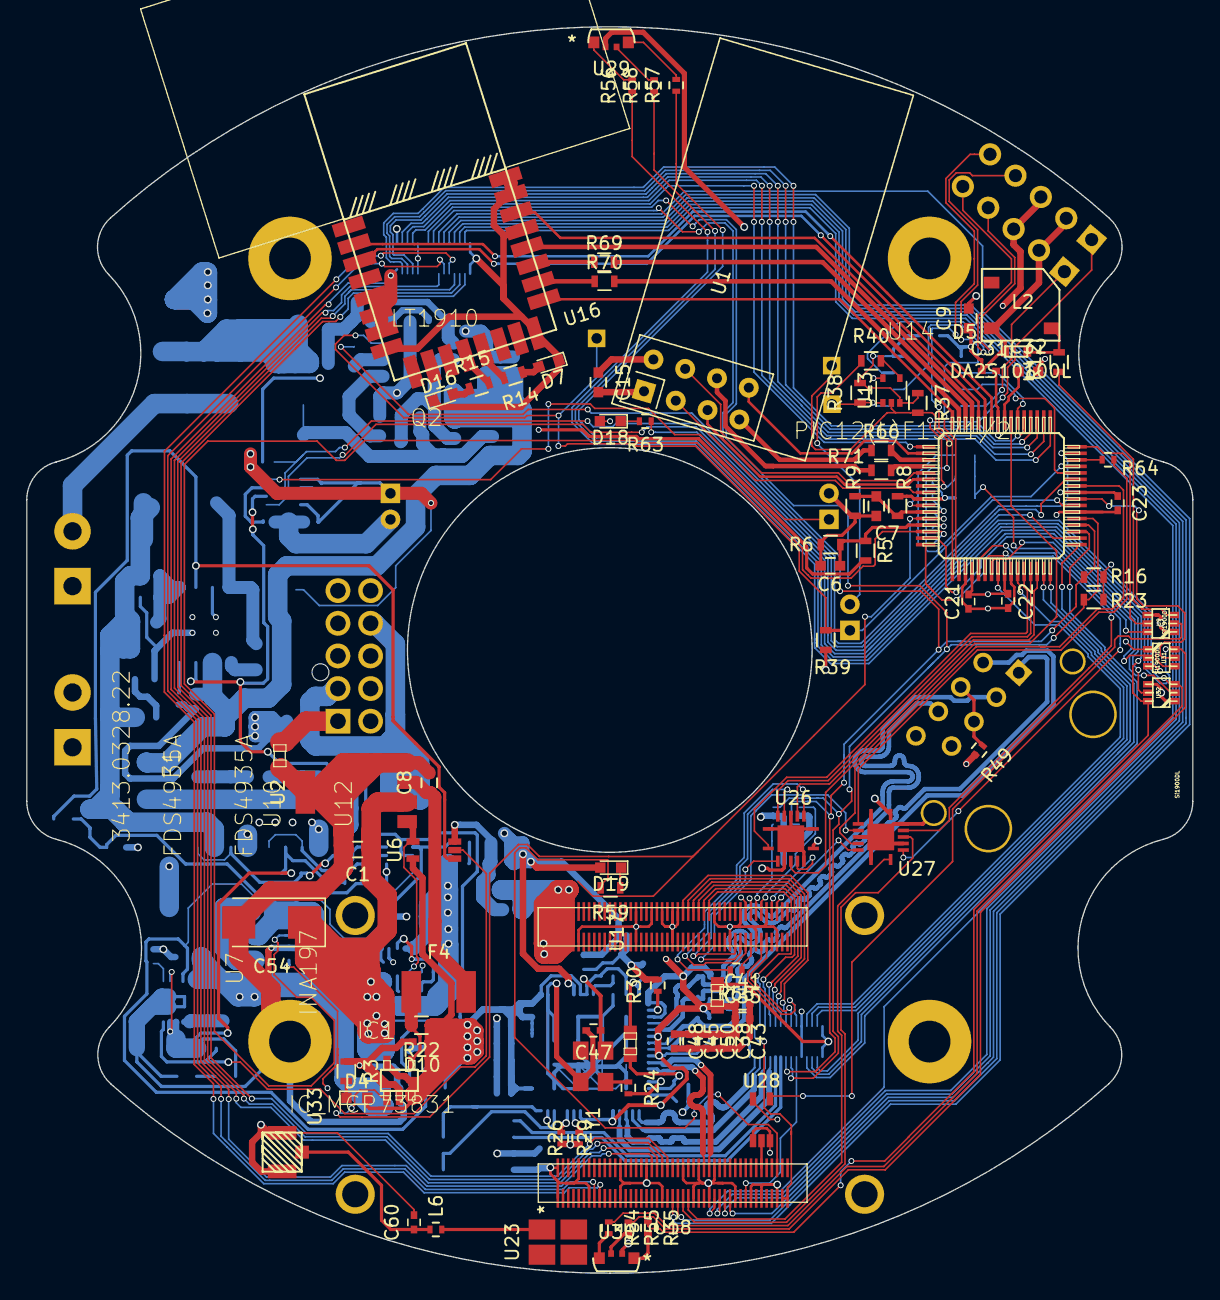
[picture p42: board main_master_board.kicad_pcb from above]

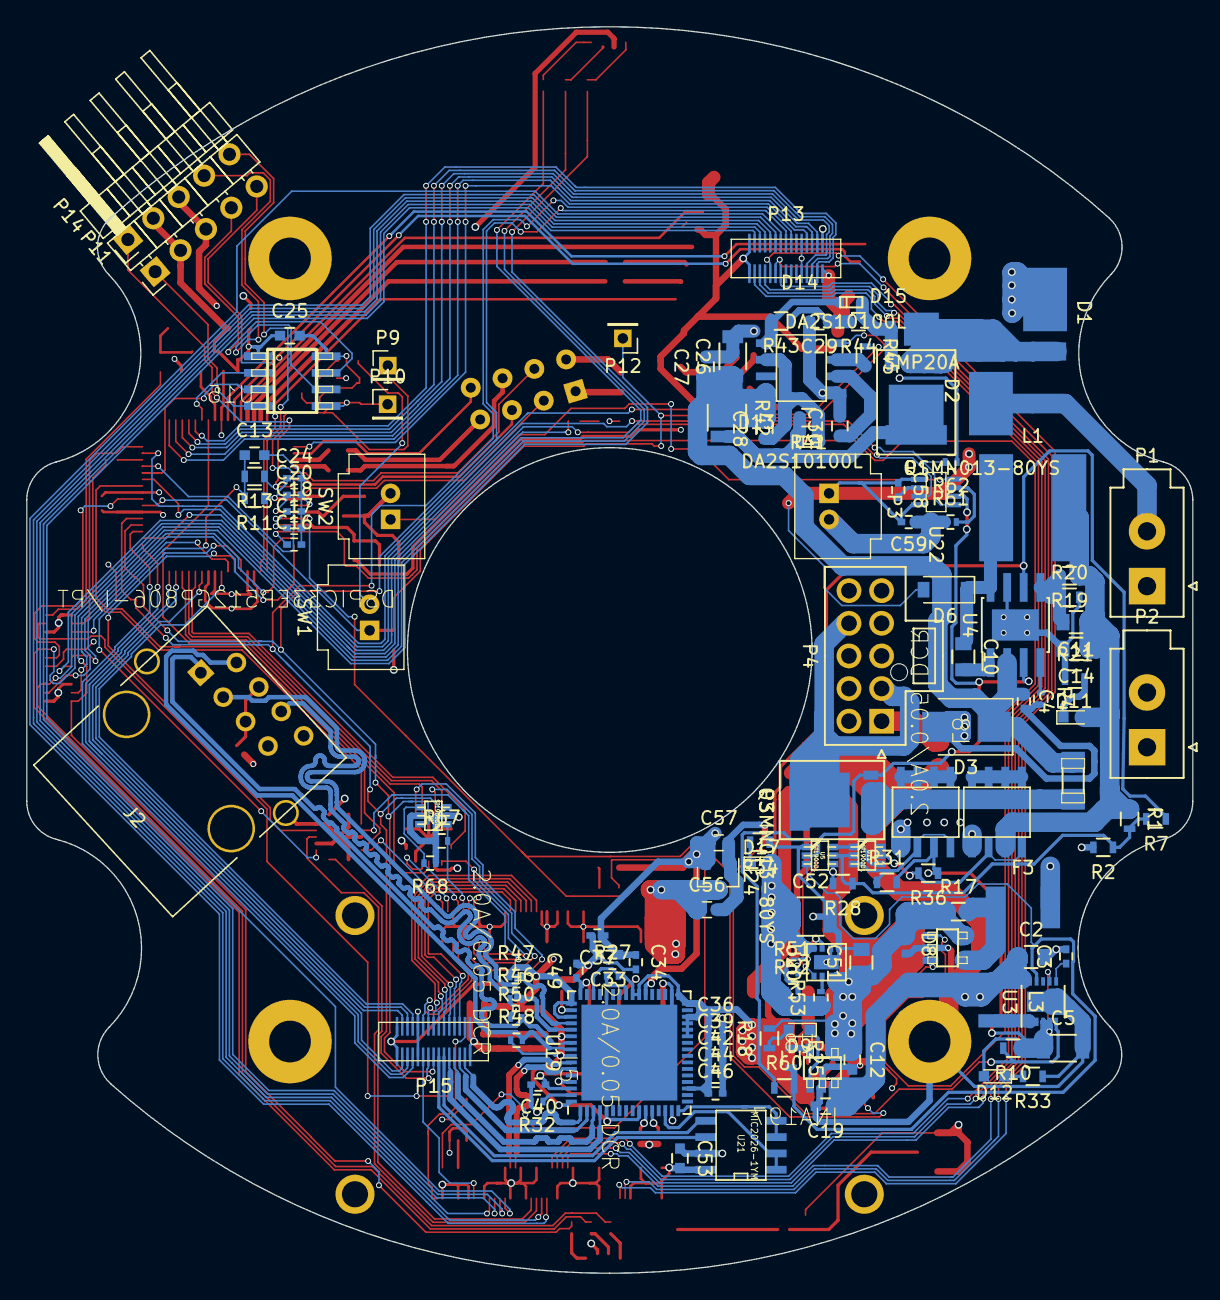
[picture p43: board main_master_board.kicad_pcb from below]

Board: 4 copper layers, 89.3 x 95.5 mm, 215 parts (123 on the bottom side), 203 nets.

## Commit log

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2016-10-18 Added altium converted files. Use only for reference!
    [0.dat.step, 1.dat.step, 10.dat.step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]
2016-10-20 Started working on the pcb and schematics for the main board on SUPERball v2
    [main_master_board.kicad_pcb, main_master_board.sch]
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2016-12-29 Added libraries for the Bucks we will be using
    [_saved_main_master_board.sch]
2016-12-29 Didn't save before pushing the last commit
    [Power_conversion.sch, _saved_main_master_board.sch, main_master_board.sch]
2016-12-29 Added power conversions for 12, 5, 3.3 from 24V
    [Power_conversion.sch, main_master_board.sch]
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2017-01-03 Finished Boost and working on power switching. LDO needs to be changed
    [Power_conversion.sch, main_master_board.sch]
2017-01-05 Added Power Board library from SBv1 and updated the power sch and started saftey switches
    [Power_Saftey_Switches.sch, Power_conversion.sch, main_master_board.sch]
2017-01-05 Made a sheet for battery connectors and found diodes for current protection during back driving
    [Battery_inputs.sch, Power_Saftey_Switches.sch, Power_conversion.sch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]
2017-01-09 Added lots of things. current/voltage monitoring. and other stuff
    [Battery_inputs.sch, Power_Saftey_Switches.sch, Power_conversion.sch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]
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2017-01-10 Updated some of the schematics and started assigning footprints
    [12_5_Buck_BOM.xls, Power_Saftey_Switches.sch, Power_conversion.sch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]
2017-01-10 Added the BOM for 24 to 12 buck
    [24_12_Buck_BOM.xls]
2017-01-10 Updating the footprints and components list. still working on it
    [Power_Saftey_Switches.sch, Power_conversion.sch, main_master_board.sch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]
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2017-01-14 Updated the project to no longer suppor the 12V Eragon board
    [24_5_Buck_BOM.xls, 4_5V_Boost_BOM.xls, Power_Saftey_Switches.sch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]
2017-01-14 Didn't save before pushing last commit
    [Power_Saftey_Switches.sch, Power_conversion.sch, _saved_Power_conversion.sch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]
2017-01-16 Moved library files to dedicated folder. Added support for Edison and Open-Q 410 boards.
    [Edison_DXF.dxf, H38489-005_R02 _emn.stp, Power_Saftey_Switches.sch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]
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2017-01-18 Started adding support for a new snapdragon board. Dart0410
    [DART-SD410_REV_1-0.dxf, Power_Saftey_Switches.sch, Power_conversion.sch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]
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2017-01-19 Started working on design and layout for fulll board with dart410. Added Macrofab libraries
    [Power_Saftey_Switches.sch, Power_conversion.sch, connectors.sch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]
2017-01-24 Added a lot of things. Put a 5v to 4v buck as well as supporing the snapdragon board
    [5_4V.xls, Power_Saftey_Switches.sch, Power_conversion.sch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]
2017-01-24 Cleaned up some wires and moved connectors out to main page. Also added some LEDs
    [Power_Saftey_Switches.sch, Power_conversion.sch, connectors.sch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]
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2017-01-26 Routed the 24-5 buck and added the dart board footprint
    [Power_Saftey_Switches.sch, Power_conversion.sch, expansion_board.sch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]
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2017-01-31 Updated the RJ45 to through hole. Moved connectors about
    [Power_Saftey_Switches.sch, Power_conversion.sch, main_master_board.kicad_pcb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]
2017-02-01 Addind support for a push button start and stop
    [Power_Saftey_Switches.sch, Power_conversion.sch, main_master_board.kicad_pcb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]
2017-02-02 Working on routing near n-p mosfets. save point incase new apporach doesn't work out
    [Power_Saftey_Switches.sch, Power_conversion.sch, main_master_board.kicad_pcb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]
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2017-02-03 Changed expansion connector to two connectors. Routed 5 to 4 buck.
    [Power_Saftey_Switches.sch, main_master_board.kicad_pcb, main_master_board.sch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]
2017-02-04 Added antenna for DART board. Also fixed 90 pin connector placement (was 180 degrees wrong). Placed Dart Board in position.
    [Power_Saftey_Switches.sch, Power_conversion.sch, main_master_board.kicad_pcb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]
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2017-02-08 Placed all compnenets on board. Now need to route!
    [Power_Saftey_Switches.sch, _saved_Power_conversion.sch, _saved_snapdragon_edison.sch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]
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2017-02-09 Updated files to support 3d rendering in KiCAD 3D viewer.
    [Power_Saftey_Switches.sch, Power_conversion.sch, main_master_board.kicad_pcb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]
2017-02-10 Messed up and routed the lan9512 is a bad spot.
    [main_master_board.kicad_pcb, main_master_board.sch, snapdragon_edison.sch]
2017-02-13 Working on routing all of the DART board
    [main_master_board.kicad_pcb, main_master_board.sch, snapdragon_edison.sch]
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2017-02-15 Added microclasp wrl files and re-routing USB and Ethernet for correct impedance traces
    [main_master_board.kicad_pcb]
2017-02-17 Routing the RGB leds. Also finished the dwm and nrf24L01
    [Power_Saftey_Switches.sch, Power_conversion.sch, main_master_board.kicad_pcb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]
2017-02-17 trying to fix the ehternet port. Got deleted at some point.
    [main_master_board.kicad_pcb]
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2017-02-17 Routed most board signals. GPIO signals left for expansion connectors.
    [main_master_board.kicad_pcb]
2017-02-21 Finished Routing!!! DRC issues, but not sure if that is really an issue...
    [Power_Saftey_Switches.sch, main_master_board.kicad_pcb, main_master_board.sch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]
2017-02-22 Added 3d file for last microclasp. Also made minor value changes. Need to switch the DWM and nRF modules...
    [Power_Saftey_Switches.sch, Power_conversion.sch, main_master_board.kicad_pcb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]
2017-02-24 switched the DWM and nRF chips. Need to finish re-routing IO pins to dsPIC
    [main_master_board.kicad_pcb]
2017-02-24 Changed the TVS diode on the 24v switching mosfet from 12A to 20A
    [Power_Saftey_Switches.sch]
2017-02-24 Finished re-routing after DWM and nRF move. Generated and committed gerber files
    [main_master_board-B.Cu.gbr, main_master_board-B.Mask.gbr, main_master_board-B.Paste.gbr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]
2017-02-27 Added new Molex antenna. Also fixed some issues where file saves were inconsistent.
    [main_master_board-B.Cu.gbr, main_master_board-B.Mask.gbr, main_master_board-B.Paste.gbr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]
2017-02-28 Fixing minor routing issues. Also compiled BoM files for parts and positions as well as moved to different Gerber extension format for MacroFab.
    [main_master_board-B.Cu.gbl, main_master_board-B.Cu.gbr, main_master_board-B.Mask.gbr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]
2017-03-02 Minor fixes to routing.
    [main_master_board-B.Cu.gbl, main_master_board-B.Mask.gbs, main_master_board-B.Paste.gbp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]
2017-03-06 Added 0ohm resistors to MISO and MOSI lines for DWM and nRF modules.
    [main_master_board.kicad_pcb, uC_and_Sensors.sch]
2017-03-07 Added resistors on PCB and recreated gerbers and xyz file
    [main_master_board-B.Cu.gbl, main_master_board-B.Mask.gbs, main_master_board-B.Paste.gbp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]
2017-05-21 started creating smaller dev boards of main board
    [Power_conversion.sch, power_24_to_5.kicad_pcb, power_24_to_5.sch]
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2017-05-22 Generated gerber files for 24_to_5 and power_switch dev boards
    [power_24_to_5.kicad_pcb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]
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2017-05-23 Modifying power switch dev board so that tracing and pads are bigger to make soldering easier.
    [power_on_switch.kicad_pcb, power_on_switch.sch]
2017-05-24 Redesigned 24 to 5 dev board
    [power_24_to_5.kicad_pcb, power_24_to_5.sch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]
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2017-10-30 Not much. Just made some variables invisible within the power sheet sch.
    [Power_Saftey_Switches.sch, Power_conversion.sch, main_master_board.sch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]
